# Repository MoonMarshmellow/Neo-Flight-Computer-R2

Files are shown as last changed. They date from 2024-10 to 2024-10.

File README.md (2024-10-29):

## NEO Flight Computer Schematics
These are the schematics for the NEO dual deploy flight computer.

### Features
- IMU For inertial positioning and acceleration data.
- Barometer for barometric altitude.
- 2 Pyrotechnic channels for charge deployment.
- Support for up to 12V Powersupply.
- Intergrated Flash Storage and SD Card for Data logging (optional)
- Battery Voltage Reader
- Almost all components are through-hole soldered for ease of assembly without solder paste.
- Support for various adafruit IMUs or Barometers.
- Small footprint (55x100mm) to keep manufacturing cheap.
- LED/Buzzer for output
- I2C/SPI Expansion Slots

### Main components:
Full BOM is in the repo.
- Arduino NANO processor (widely available and easily programmable, low memory so libraries that can be used are limited (can be used with the Nano Every, which has more memory))
- Adafruit BMP388 breakout board (compatible with almost all adafruit Barometer boards)
- Adafruit ICM20649 IMU (compatible with almost all adafruit IMU boards)
- Micro SD card socket
- W25Q32FV Winbond Flash Storage Chip (compatible with other similar pinout chips like the SST25VF064C from Microchip)

### Firmware
Firmware for the board is a work in progress, but the board is compatible with all main Arduino Libraries for each sensor and the SD and Flash Chip. Writing simple software for launch and apogee detection isn't too difficult.

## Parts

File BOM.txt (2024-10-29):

Partlist exported from C:/Users/katzi/Documents/EAGLE/projects/NEO_R2/Inceptor_Schematic.sch at 24/02/2024 13:05

Qty Value                     Device                    Package             Parts          Description                                                MF MPN OC_FARNELL OC_NEWARK POPULARITY PROD_ID    SF_SKU    SPICEPREFIX VALUE   
1                             ARDUINO_NANO              ARDUINO_NANO        ARDUINO_NANO1  Arduino Nano V3.0                                                                                                                          
2                             MOSFET-NREFLOW            SOT23               Q1, Q2         N-Channel Mosfet                                                                                                                           
2                             W237-4                    W237-4              X3, X4         WAGO SCREW CLAMP                                                  unknown    unknown   10                                                  
1   0.1uf                     C-EU025-024X044           C025-024X044        C1             CAPACITOR, European symbol                                                             56                              C                   
1   100K                      R-US_0207/7               0207/7              R10            RESISTOR, American symbol                                                                                                                  
1   10M                       R-US_0207/7               0207/7              R1             RESISTOR, American symbol                                                                                                                  
1   10ohm                     R-US_0207/7               0207/7              R8             RESISTOR, American symbol                                                                                                                  
1   10uf                      C-EU025-024X044           C025-024X044        C2             CAPACITOR, European symbol                                                             56                              C                   
1   1M                        R-US_0207/7               0207/7              R9             RESISTOR, American symbol                                                                                                                  
3   1ohm                      R-US_0207/7               0207/7              R2, R4, R7     RESISTOR, American symbol                                                                                                                  
1   22pF                      C-EU025-024X044           C025-024X044        C3             CAPACITOR, European symbol                                                             56                              C                   
1   4010N                     4010N                     DIL16               IC2            Hex BUFFER, Non-inverting                                                              0                                                   
1   40ohm                     R-US_0207/7               0207/7              R6             RESISTOR, American symbol                                                                                                                  
2   470ohm                    R-US_0207/7               0207/7              R3, R5         RESISTOR, American symbol                                                                                                                  
1   7805TV                    7805TV                    TO220V              IC1            Positive VOLTAGE REGULATOR                                                             57                                                  
1   BMP388                    BMP388                    BMP388              U$3                                                                                                                                                       
1   BUZZER-PTH                BUZZER-PTH                BUZZER-12MM         LS1            Buzzer                                                                                            COMP-08253 COM-07950                     
4   CON_TERMINAL_BLOCK_02-5MM CON_TERMINAL_BLOCK_02-5MM TERMINAL_BLOCK_2P_5 J1, J2, J3, J4 2 poles wire to board terminal block                                                                                                       
1   ICM20649                  ICM20649                  ICM20649            U$4                                                                                                                                                       
1   MICROSD                   MICROSD                   MICROSD             U$1            Micro-SD / Transflash card holder with SPI pinout                                                                                          
1   RGBLED_CA-5MM             RGBLED_CA-5MM             LED5MMRGB           LED1           RGB LED, common-anode5MM Staggered pins5mm Piranha package                                                                                 
1   W25Q32FV                  W25Q32FVSS                SOIC-8              U1             W25Q32FV 32Mb (4MB) Serial Flash Memory                                                           IC-13229                         W25Q32FV

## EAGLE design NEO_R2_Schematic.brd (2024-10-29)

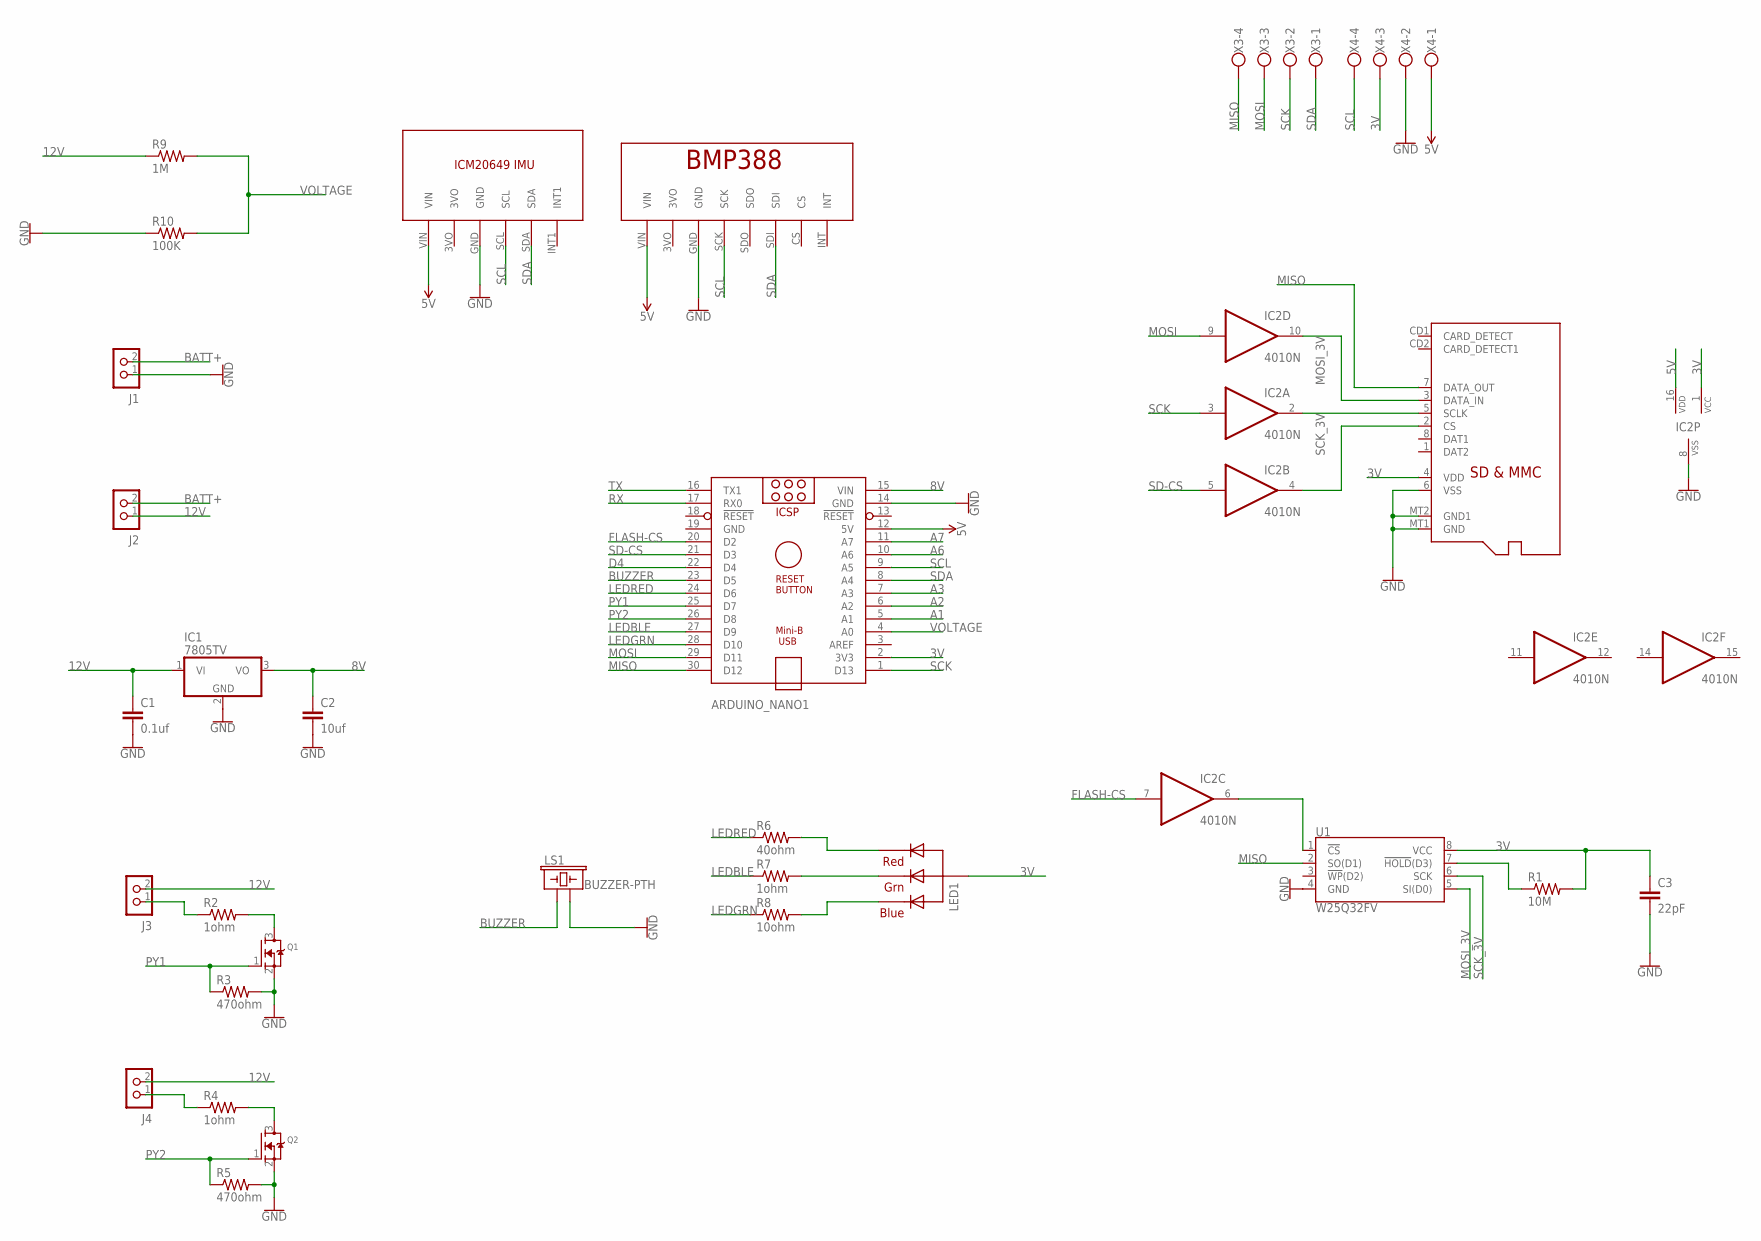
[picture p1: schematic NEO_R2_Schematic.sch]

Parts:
ARDUINO_NANO1: ARDUINO_NANO
C1: 0.1uf; C025-024X044
C2: 10uf; C025-024X044
C3: 22pF; C025-024X044
IC1: 7805TV; TO220V
IC2: 4010N; DIL16
J1, J2, J3, J4: CON_TERMINAL_BLOCK_02-5MM; TERMINAL_BLOCK_2P_5
LED1: RGBLED_CA-5MM; LED5MMRGB
LS1: BUZZER-PTH; BUZZER-12MM
Q1, Q2: MOSFET-NREFLOW; SOT23
R1: 10M; 0207/7
R2, R4, R7: 1ohm; 0207/7
R3, R5: 470ohm; 0207/7
R6: 40ohm; 0207/7
R8: 10ohm; 0207/7
R9: 1M; 0207/7
R10: 100K; 0207/7
U1: W25Q32FV; SOIC-8
U$1: MICROSD
U$3: BMP388
U$4: ICM20649
X3, X4: W237-4

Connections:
3V: ARDUINO_NANO1.2 (3V3), C3.1, IC2.1 (VCC), LED1.2 (VCC), R1.2, U1.8 (VCC), U$1.4 (VDD), X4.3
5V: ARDUINO_NANO1.12 (5V), IC2.16 (VDD), U$3.VIN, U$4.VIN, X4.1
8V: ARDUINO_NANO1.15 (VIN), C2.1, IC1.3 (VO)
12V: C1.1, IC1.1 (VI), J2.1, J3.2, J4.2, R9.1
A1: ARDUINO_NANO1.5 (A1)
A2: ARDUINO_NANO1.6 (A2)
A3: ARDUINO_NANO1.7 (A3)
A6: ARDUINO_NANO1.10 (A6)
A7: ARDUINO_NANO1.11 (A7)
BATT+: J1.2, J2.2
BUZZER: ARDUINO_NANO1.23 (D5), LS1.+ (1)
D4: ARDUINO_NANO1.22 (D4)
FLASH-CS: ARDUINO_NANO1.20 (D2), IC2.7 (I)
GND: ARDUINO_NANO1.14 (GND), ARDUINO_NANO1.19 (GND), C1.2, C2.2, C3.2, IC1.2 (GND), IC2.8 (VSS), J1.1, LS1.- (2), Q1.2 (S), Q2.2 (S), R3.2, R5.2, R10.1, U1.4 (GND), U$1.6 (VSS), U$1.MT1 (GND), U$1.MT2 (GND1), U$3.GND, U$4.GND, X4.2
LEDBLE: ARDUINO_NANO1.27 (D9), R7.1
LEDGRN: ARDUINO_NANO1.28 (D10), R8.1
LEDRED: ARDUINO_NANO1.24 (D6), R6.1
MISO: ARDUINO_NANO1.30 (D12), U1.2 (SO(D1)), U$1.7 (DATA_OUT), X3.4
MOSI: ARDUINO_NANO1.29 (D11), IC2.9 (I), X3.3
MOSI_3V: IC2.10 (O), U1.5 (SI(D0)), U$1.3 (DATA_IN)
unnamed: R1.1, U1.7 (!HOLD!(D3))
unnamed: J3.1, R2.1
unnamed: Q1.3 (D), R2.2
unnamed: J4.1, R4.1
unnamed: Q2.3 (D), R4.2
unnamed: IC2.4 (O), U$1.2 (CS)
unnamed: LED1.1 (RED), R6.2
unnamed: LED1.3 (GREEN), R7.2
unnamed: LED1.4 (BLUE), R8.2
unnamed: IC2.6 (O), U1.1 (!CS!)
PY1: ARDUINO_NANO1.25 (D7), Q1.1 (G), R3.1
PY2: ARDUINO_NANO1.26 (D8), Q2.1 (G), R5.1
RX: ARDUINO_NANO1.17 (RX0)
SCK: ARDUINO_NANO1.1 (D13), IC2.3 (I), X3.2
SCK_3V: IC2.2 (O), U1.6 (SCK), U$1.5 (SCLK)
SCL: ARDUINO_NANO1.9 (A5), U$3.SCK, U$4.SCL, X4.4
SD-CS: ARDUINO_NANO1.21 (D3), IC2.5 (I)
SDA: ARDUINO_NANO1.8 (A4), U$3.SDI, U$4.SDA, X3.1
TX: ARDUINO_NANO1.16 (TX1)
VOLTAGE: ARDUINO_NANO1.4 (A0), R9.2, R10.2

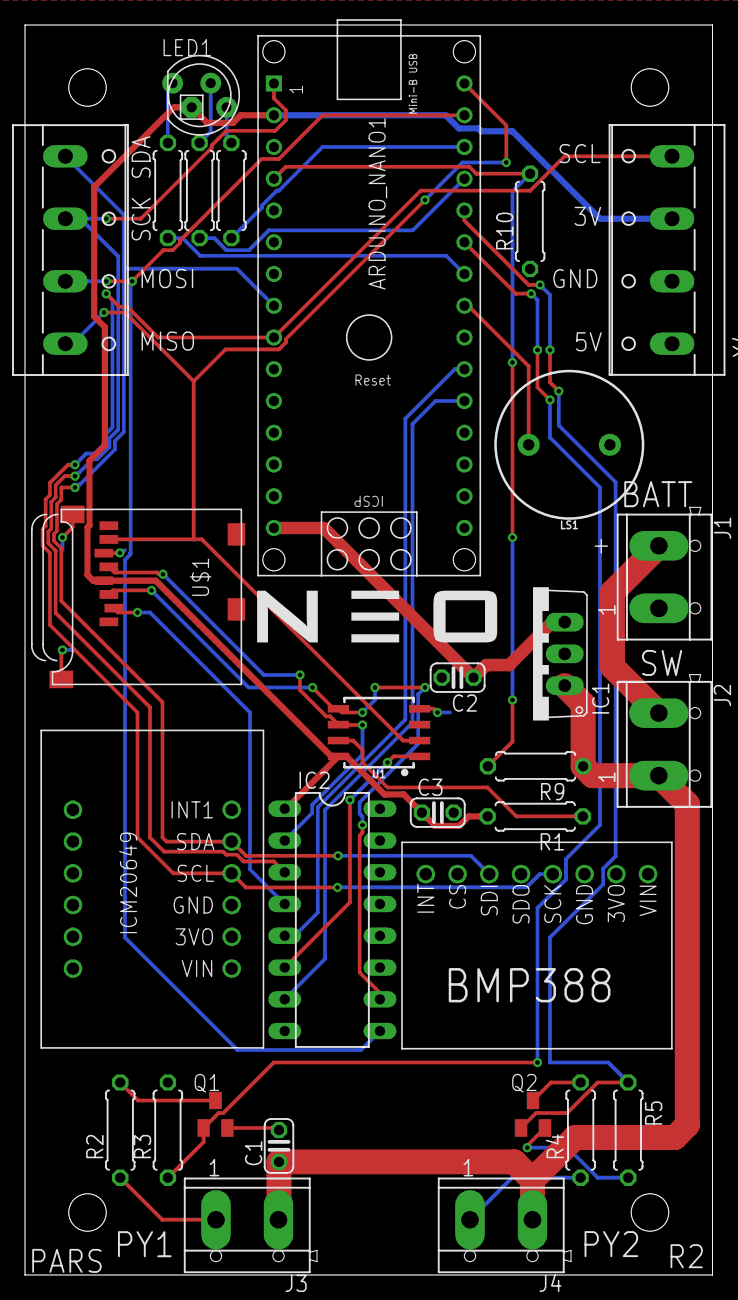
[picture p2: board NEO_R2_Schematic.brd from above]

Board: 2 copper layers, 55.0 x 100.0 mm, 30 parts (0 on the bottom side), 32 nets.

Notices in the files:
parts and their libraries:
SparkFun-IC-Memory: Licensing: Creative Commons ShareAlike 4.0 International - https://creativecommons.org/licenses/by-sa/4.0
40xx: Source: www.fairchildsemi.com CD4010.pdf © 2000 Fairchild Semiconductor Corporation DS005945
